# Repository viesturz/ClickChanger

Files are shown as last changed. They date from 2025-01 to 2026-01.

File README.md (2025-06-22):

# What is this?

A minimalistic 3d printer toolhead design, build from ground up for tool changing and primarily the Voron Family of printers.
Inspired by [Tapchanger](https://github.com/viesturz/tapchanger) and [Stealthchanger](https://github.com/DraftShift/StealthChanger). But not getting into  [PitStop](https://mihaidesigns.com/pitstop3/) territory yet.

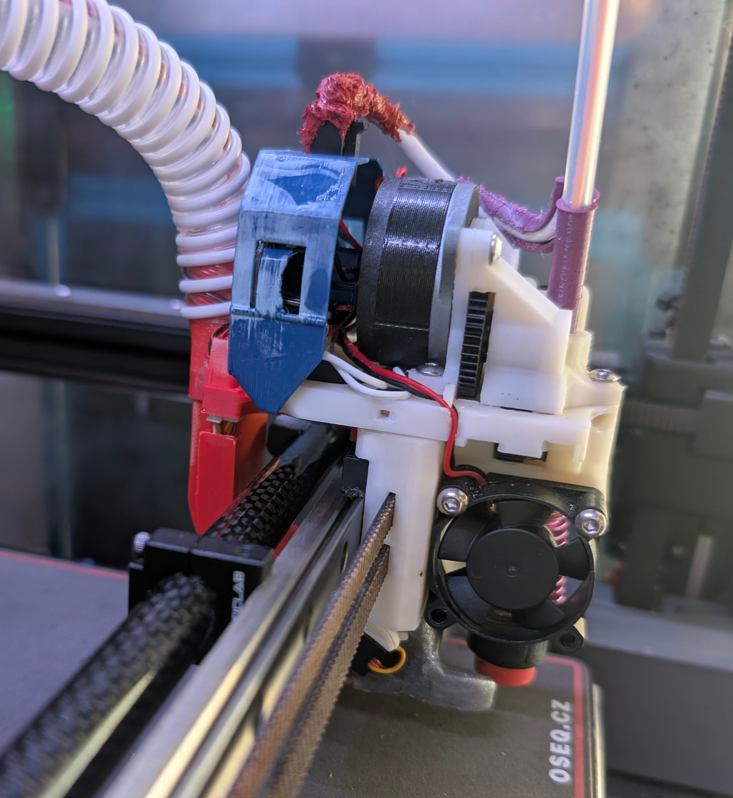
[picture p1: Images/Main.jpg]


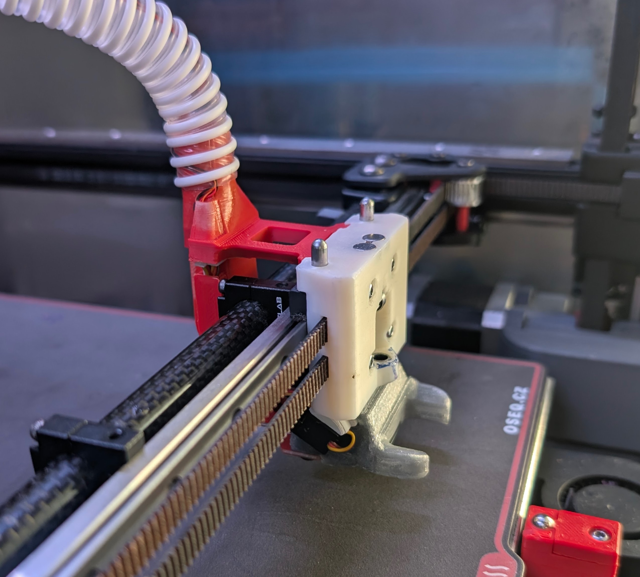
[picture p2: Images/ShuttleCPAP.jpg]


## How is this different?

ClickChanger is a yet another vertically attached design, but building on previous experiences, but here are some design directions it focuses on:
* A hotend based nozzle probe, like Revo PZ, not requiring the smooth vertical movement by the docking mechanism
* Rigid connection between the Y rail and hotend's heatsink, minimizing thermal expansion differences between toolheads
* A Shared part cooling fan integrated in the shuttle, connected via Pogo pins
* A "naked" toolhead, allowing for better cooling and overall less weight.

And keeping the features from other designs:

* Vertical motion to attach/detach the toolhead
* No wires to the shuttle, single cable to each toolhead

### Roadmap

Some of next directions this is going, in no particular order

* Documentation documentation documentation

### Contributing

Please file bugs and pull requests. My free time is quite limited, so will answer irregularly.
[Voron Toolchangers Discord](https://discord.com/invite/xmDWrYGwVJ) has lots of toolchanger users.
Also check out the [Youtube channel](https://www.youtube.com/playlist?list=PLqU7kX5nUJDT31KPcYAykZ2nuPKu_lhjn).

# Supported hotends

* Revo Voron
* Dragon or Dragon High flow
* Rapido HF (not the UHF)

# Supported bed probes
 * Revo PZ on T0
 * Beacon probe (low profile)
 * Cartographer probe (low profile)

# Supported extruders

* HGX Large Gears - personal favorite of mine, great for flexibles; lowest weight and integrated strain relief.
* HGX Large Gears V2
* Orbiter V2
* Sherpa mini and compatibles

# Supported toolboards
* Bitgtreetach EBB36 and compatibles
* Mellow Fly SHT36 V2 and Pro
* LDO Nitehawk (untested)

# BOM

**Common consumables**

* M3 screws, button head preferrably, 8mm and some other sizes
* M3x5x4 heatset inserts (voron spec)
* superglue, small tip tube, low viscosity

**Shuttle**

* a CPAP fan
* ~1m 15mm diameter tube
* a 3x6x2.5mm bearing (3x6x3 works too)
* a 2gram micro servo, DSPOWER has worked well for me
* 2 m2x4 screws
* some servo wire

**Toolhead**

* A supported extruder, toolhead, toolboard
* 1x 4mm x12mm round end steel pin
* 2x 4x6x6 mm bushing; preferrably the hybrid bushings for smoother slide
* a Kailh Micro switch or compatible 3mm tall momentary switch
* 30x30x10 or 30x30x7 axial fan for hotend cooling
* 1x m2x6 **socket head** screw
* 2x 6x3mm magnets

**Dock**

* 30 mm of 7x0.1mm springsteel, salvageable from 1m tape measure.
* High temp silicone for the nozzle pad

# Assembly instructions

* [CPAP valve](CPAP.md)
* See [TapChanger](https://github.com/viesturz/tapchanger) for my docking/wiring setup.
* See [Klipper-Toolchanger](https://github.com/viesturz/klipper-toolchanger/) for klipper firmware, [example config](https://github.com/viesturz/klipper-toolchanger/tree/main/examples/probe%20on%20T0).

More coming up

# Revision log

## 2.0 - CPAP is mandatory now.

Not compatible with previous versions, you will need to reprint everything, except docks and need a new microswitch.

* Only CPAP supported, the airflow is just so much better.
* More rigid shuttle, going from 6 to 8 mm width, extra side walls.
* Using a slimmer 3mm tall microswitches for tool detection
* Some supports modelled
* Remodelled PTFE tube connector
* Better toolboard cages
* Best part is no part - no more retaining clips
* Tensioning screw position adjusted for slightly less click and more tension

## 1.1.1 - Small tweaks and cleanups.

## 1.1 - CPAP edition

* CPAP and eddy current probe support.
* Docks slightly redesigned, added magnets in docks.

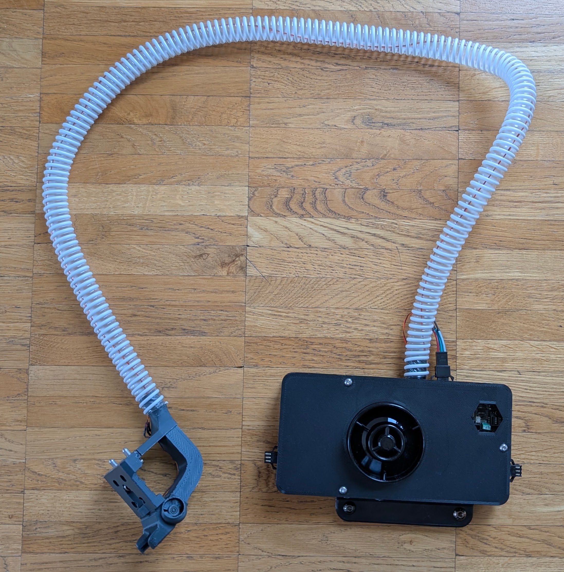
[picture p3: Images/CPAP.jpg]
CPAP
}

## 1.0 - Fingers crossed

The first one that is ready to be beta tested. **Not compatible with previous ones** the shuttle interface has changed.

Added: 
* Rigid mount dock initial version
* CPAP initial version

Small refinements across the board

## 0.9 - Small improvements

Added:

* Rapido extruder base
* Nitehawk toolbard cage

Small refinements across the board:

* HGX Lite gears 2 refinements
* Fan shroud refinements
* Better fit for some holes

## 0.8 - It prints!

Introduced pogo pins for the fan connection and a new wiring holder.

Full PTFE tube channel for HGX - better for flexibles.

Assembly is quite repeatable now.

Printing reasonably stable now, hundreads of toolchanges but still expect some warts.

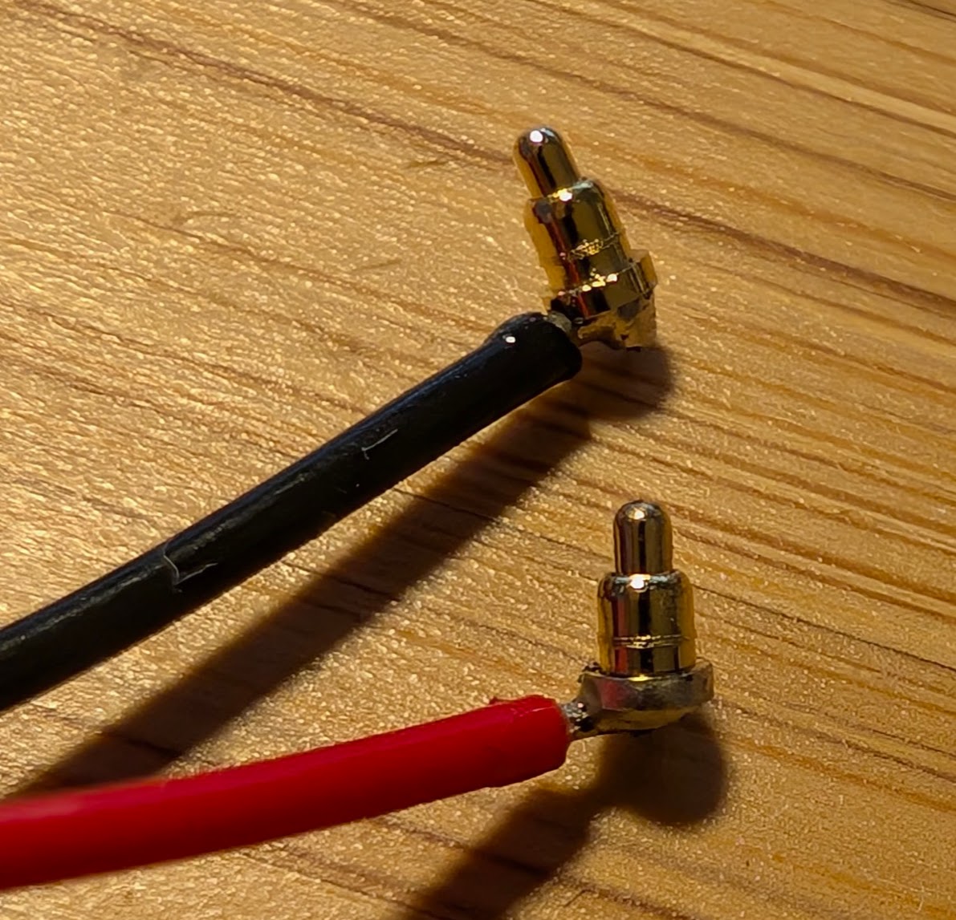
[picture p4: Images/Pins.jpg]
Pogo pins


## 0.1 - It clicks!

There is an initial BOM, the click force is good, assembly is repeatable, building two and putting to the test.

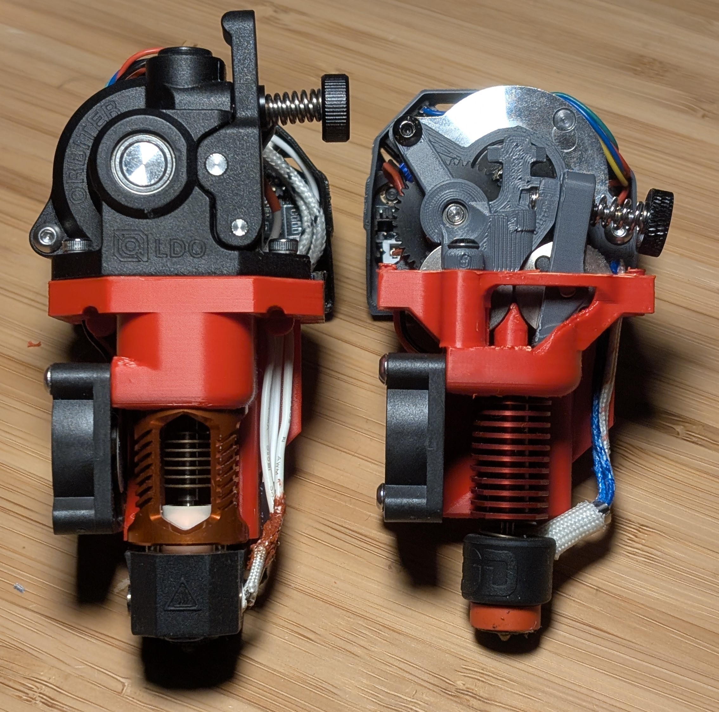
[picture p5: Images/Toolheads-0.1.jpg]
Toolheads

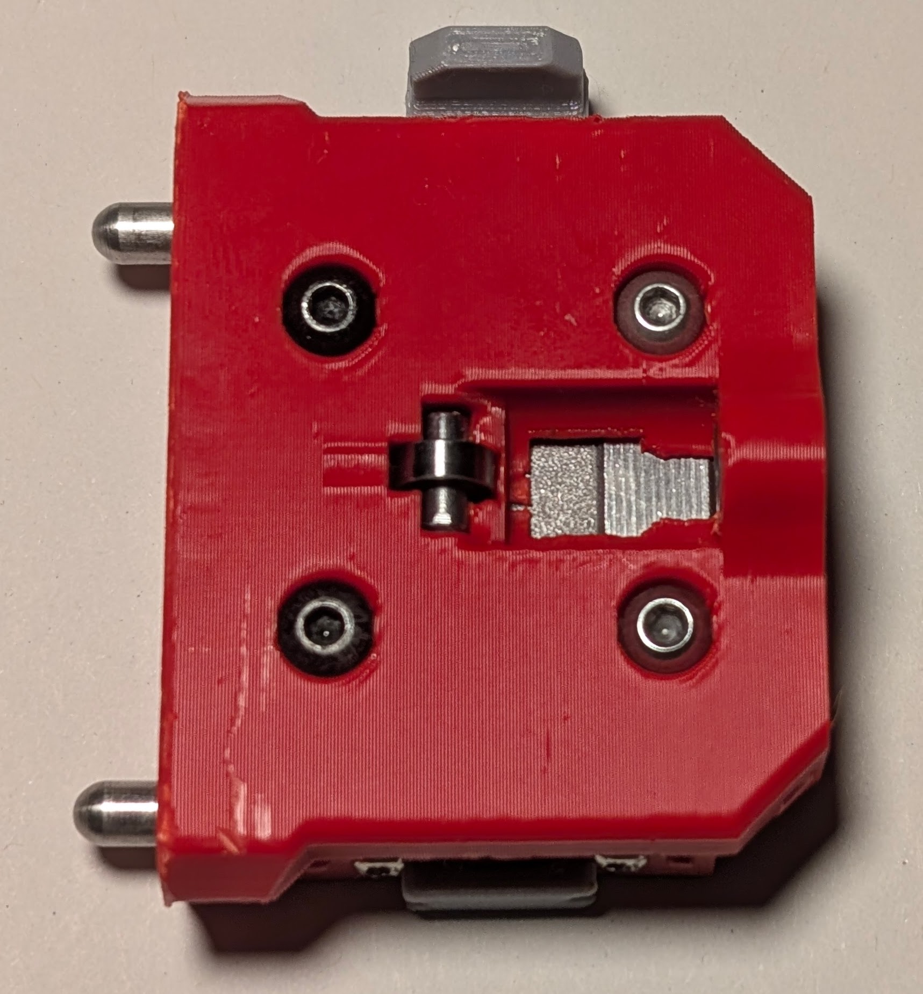
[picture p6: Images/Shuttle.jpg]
Shuttle


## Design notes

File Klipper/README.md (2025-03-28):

# Klipper integration

Please see [Klipper-Toolchanger](https://github.com/viesturz/klipper-toolchanger/)

## CPAP

Feel free to adapt my [CPAP config](./CPAP_mcu.cfg). That is based on a dedicated toolbard.
You will need to change the pin assignment if you are using something else..

Please file a bug if you are interested in detailed build instructions for the CPAP box.

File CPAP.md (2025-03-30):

# Valve installation

The valve installation is tricky by the fact that the servos have no stop point so getting the valve angle right is difficult. 

Start by powering on the servo and set the angle to 90 degrees so that it's at known angle.

Then attach the shim and press on the valve so that it aligns with the shim.
Once pressed on, secure the valve with a screw or a bit of superglue. It will rattle loose otherwise.

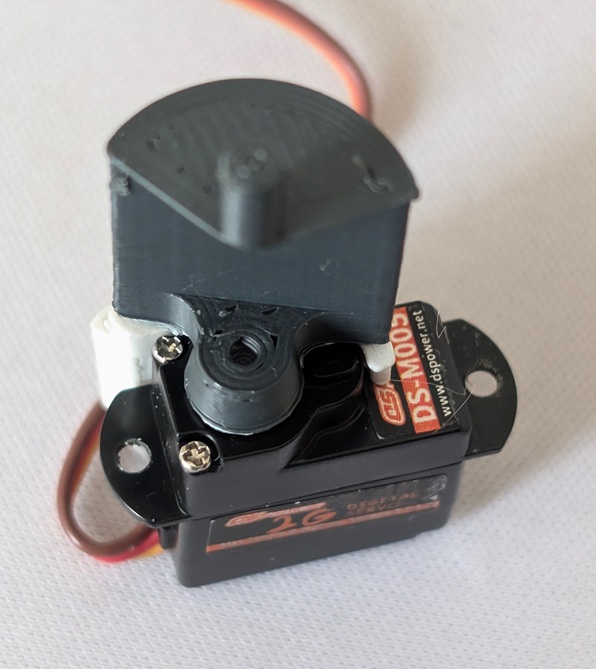
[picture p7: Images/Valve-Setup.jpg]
Valve setup


Then install the bearing on the opposite side.

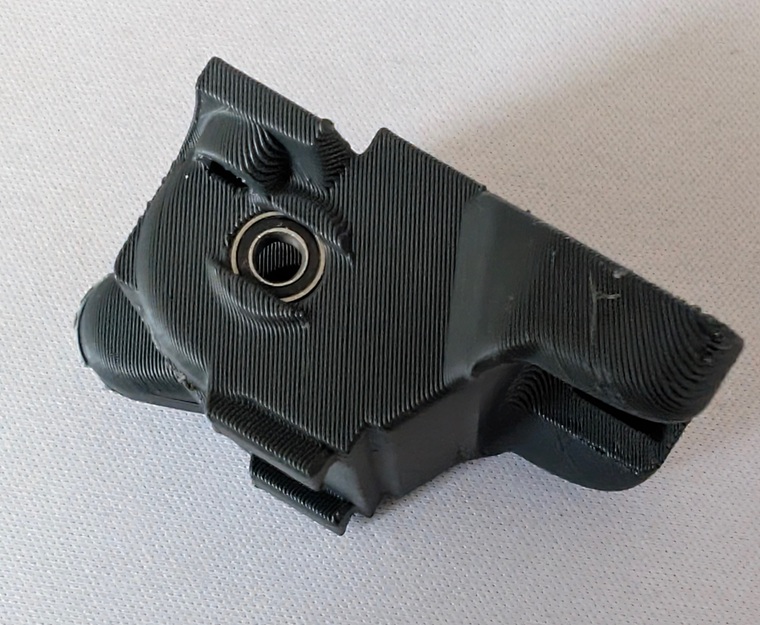
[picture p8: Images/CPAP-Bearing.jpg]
Bearing


Then carefullly push the valve assembly into the shroud. Note the servo wire routing.

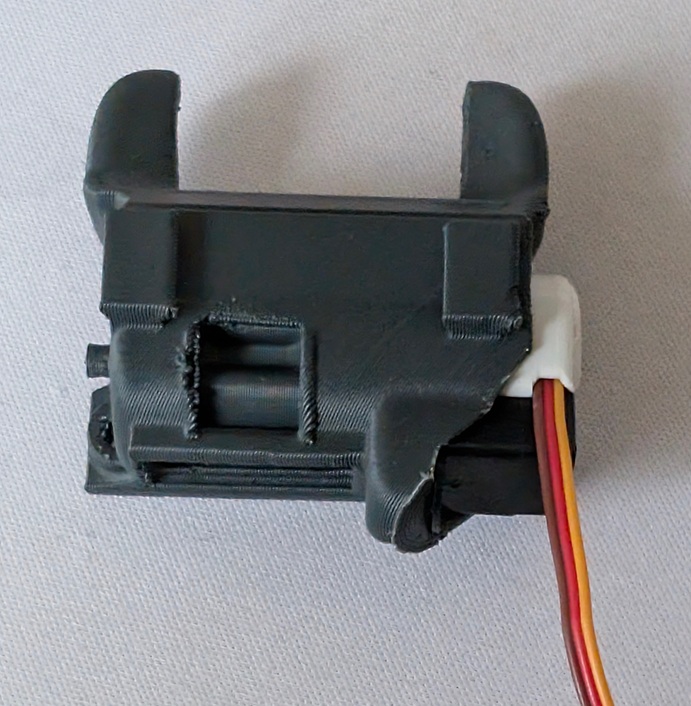
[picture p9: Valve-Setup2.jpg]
Valve assembed


And secure with 2 M2 x4 screws.

## Fine tuning the servo angle.

90 degrees is your fully open angle. And fully closed should be about 165 degrees, but will depend on your servo, so test and adjust as necessary.

See [Example klipper config](Klipper/CPAP_mcu.cfg)  for valve and CPAP control

| Valve open  | Valve closed |
| --- | --- |
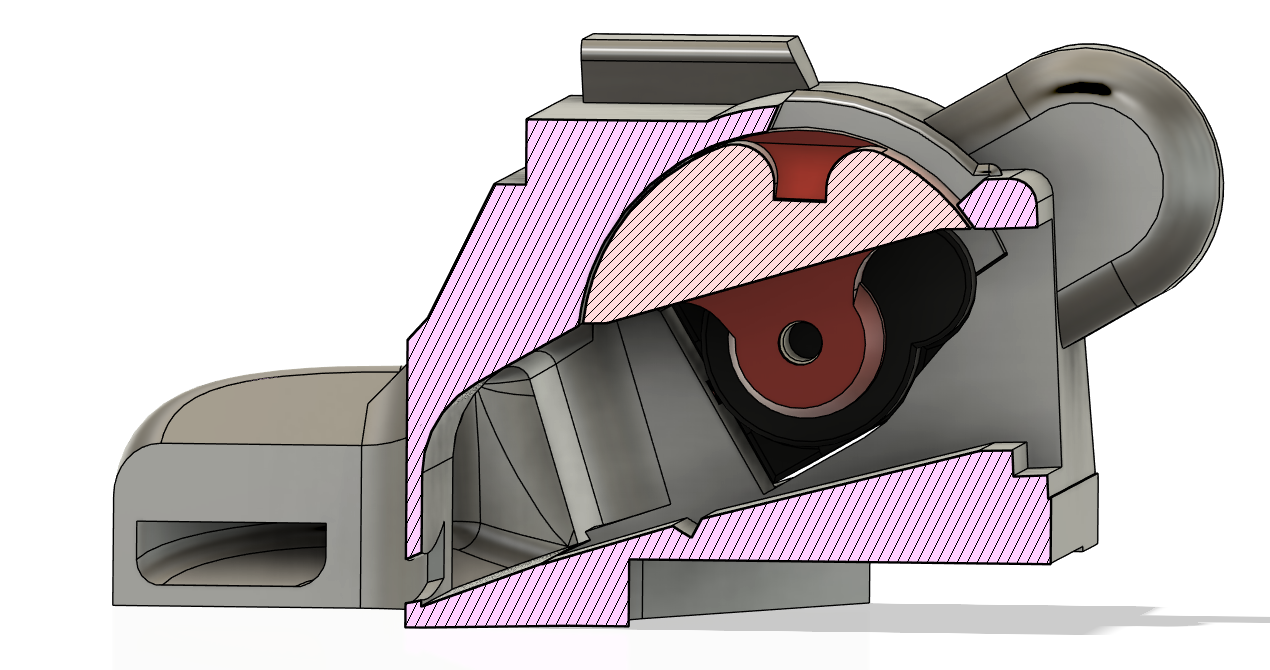
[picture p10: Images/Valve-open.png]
Open
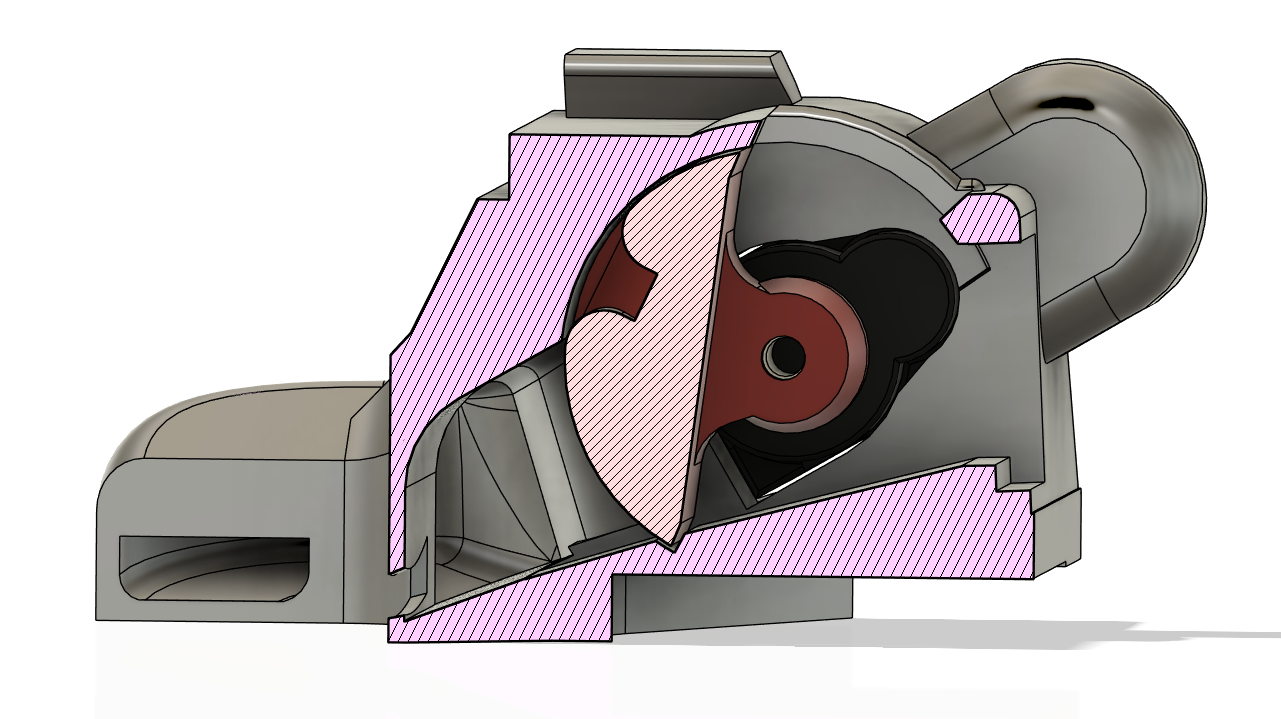
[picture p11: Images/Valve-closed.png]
Closed
|   |  |

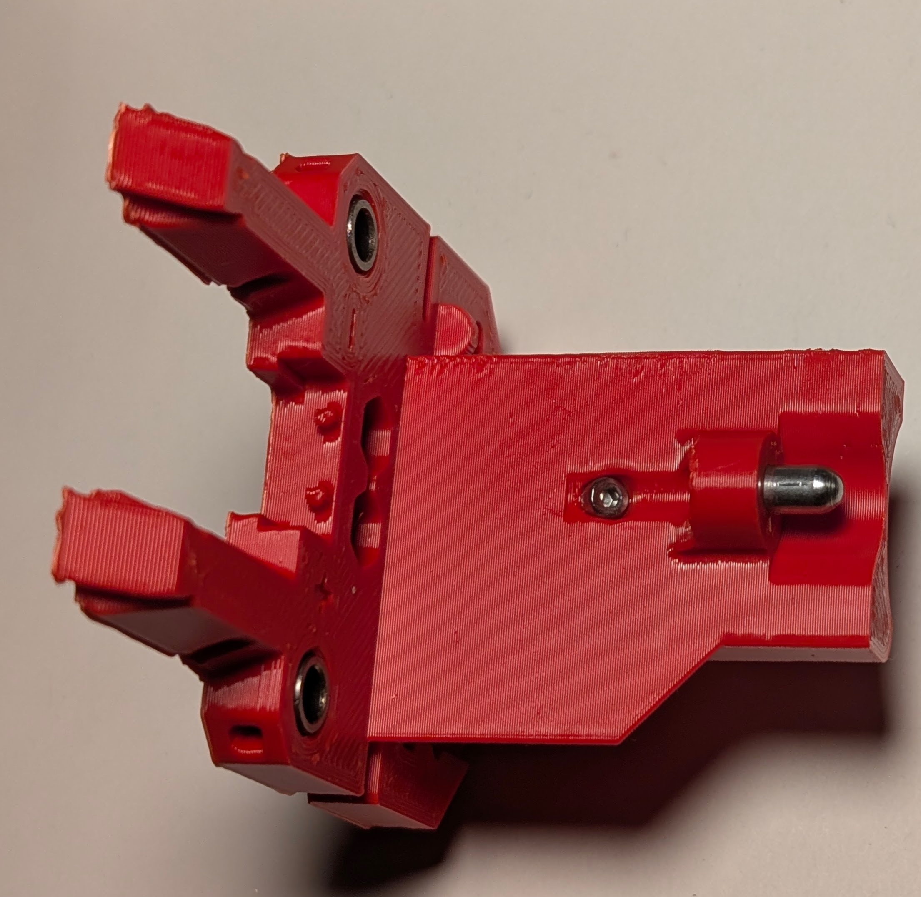
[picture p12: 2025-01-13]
Images/ToolheadPart.jpg

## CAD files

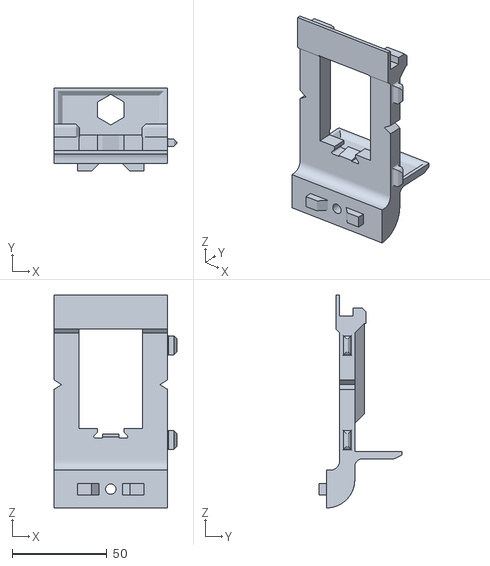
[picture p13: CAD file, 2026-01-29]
BearingsVariant/Dock/Dock Liftbar.obj
65.0 x 44.0 x 112.6

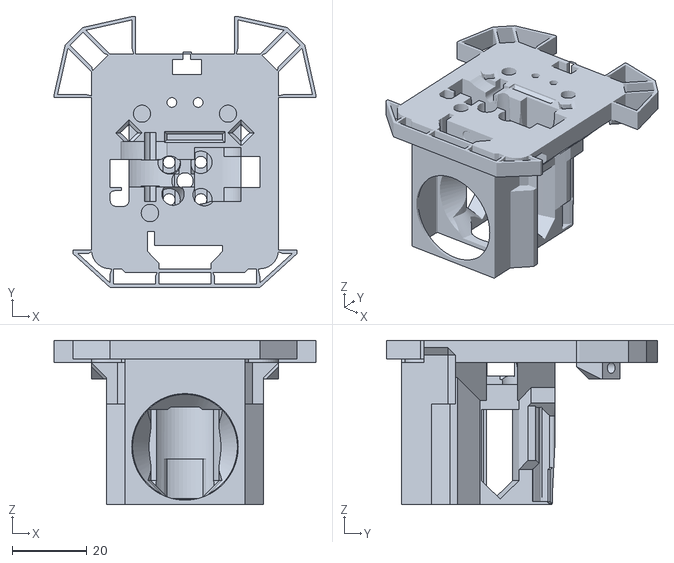
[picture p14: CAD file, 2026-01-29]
BearingsVariant/Hotends/Base Revo.obj
70.0 x 72.5 x 44.0

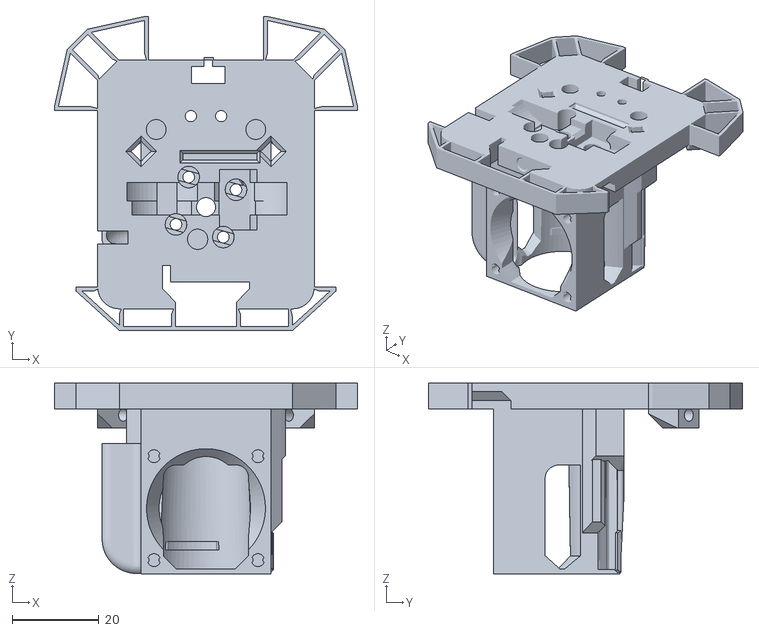
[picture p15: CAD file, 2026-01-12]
BearingsVariant/Hotends/Rapido/Base Rapido.obj
70.0 x 72.5 x 44.1

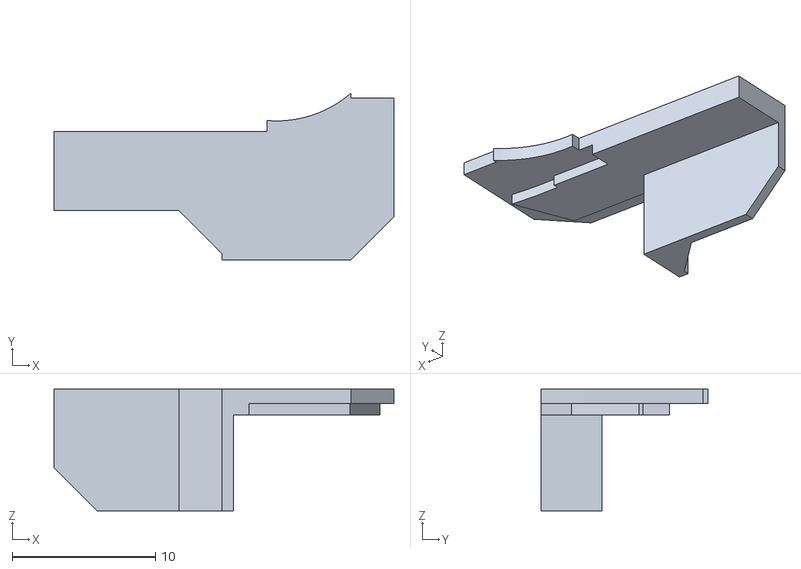
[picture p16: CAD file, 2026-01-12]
BearingsVariant/Shuttle/Wire Shield.obj
23.7 x 11.6 x 8.50

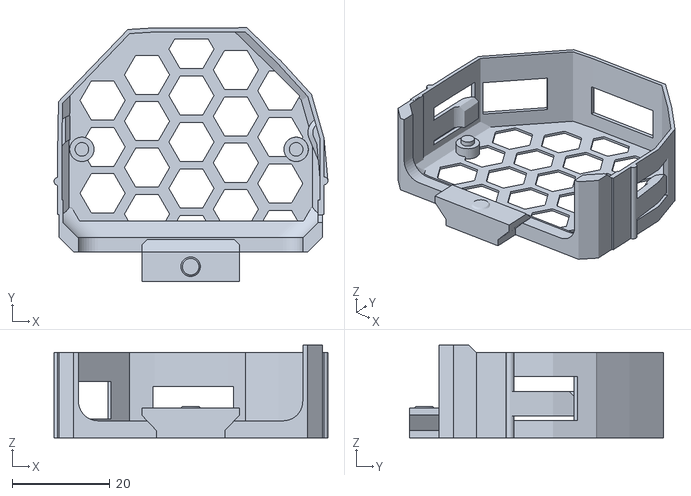
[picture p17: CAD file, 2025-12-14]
BearingsVariant/Toolbards/LDO nitehawk cage.obj
56.1 x 51.9 x 19.0

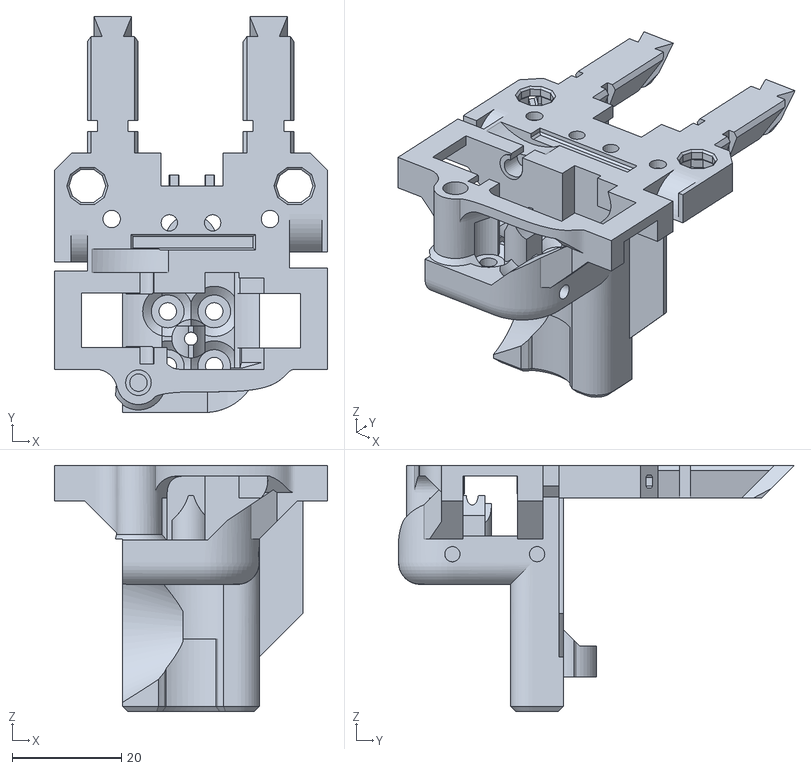
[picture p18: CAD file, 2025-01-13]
Cores/HGX Gears + Revo/Core Revo.obj
50.0 x 72.5 x 45.1

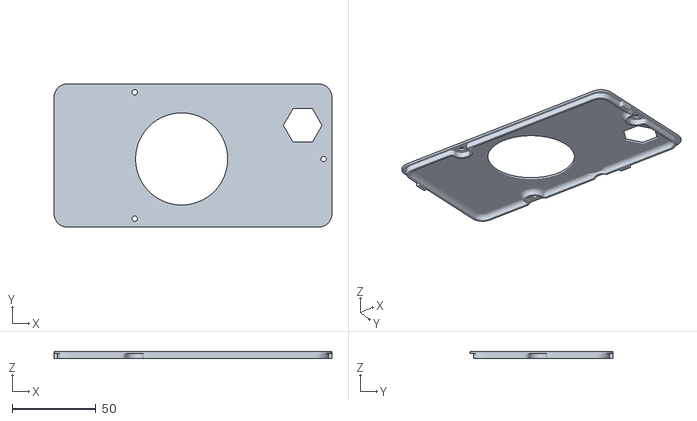
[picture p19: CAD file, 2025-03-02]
CPAP/WS7040 mount/Lid.obj
166.0 x 85.5 x 4.00

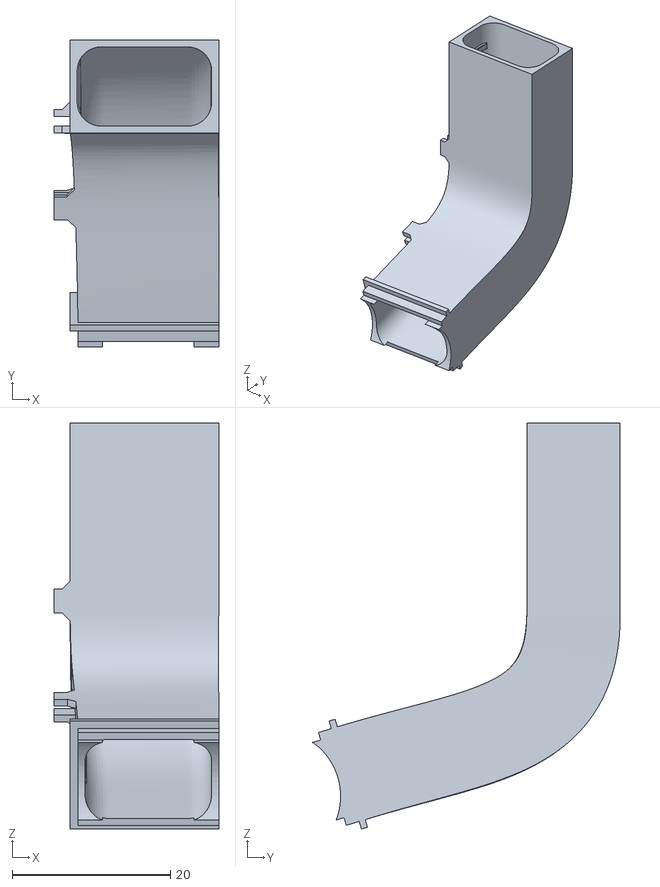
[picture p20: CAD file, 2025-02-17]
Extras/CPAP/Tube.obj
20.8 x 38.8 x 51.3

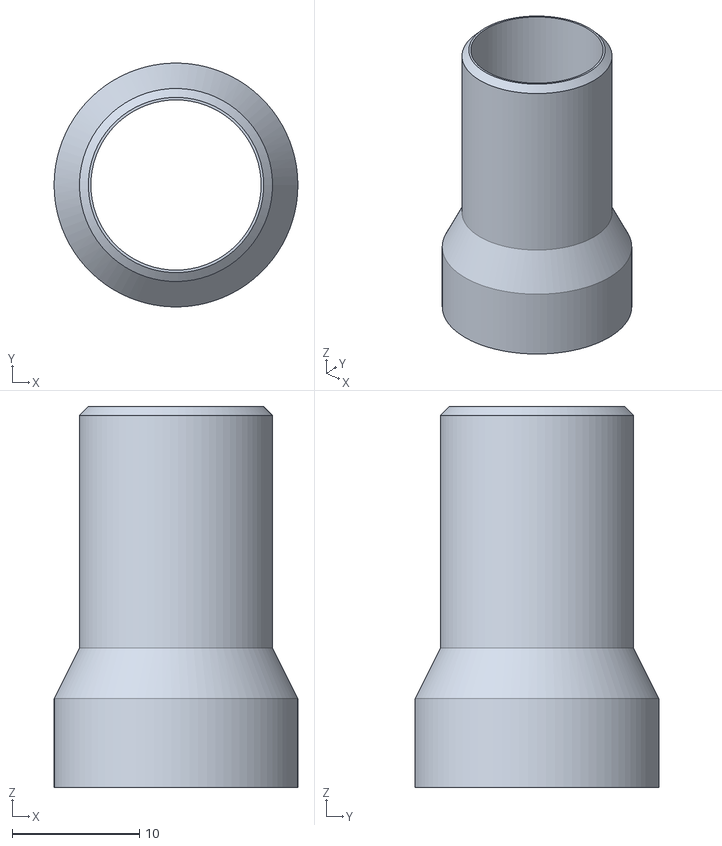
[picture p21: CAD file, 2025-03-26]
Extras/WS7040 mount/Tube Adapter.obj
19.2 x 19.2 x 30.0

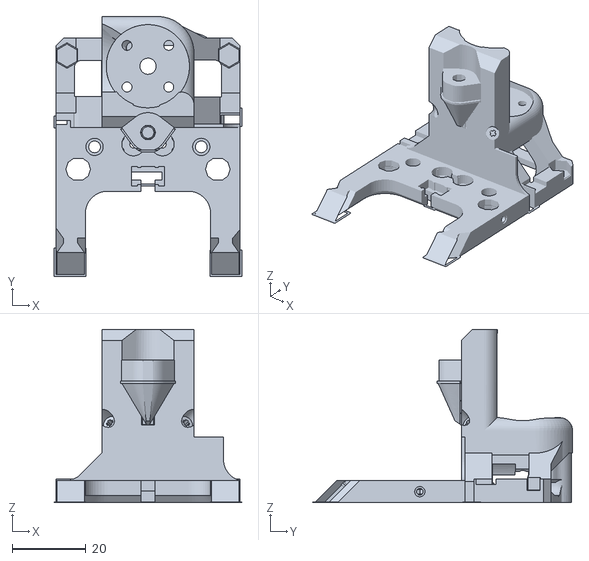
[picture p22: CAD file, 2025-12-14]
PinsVariant/Cores/Dragon + HGX Gears.obj
51.0 x 70.6 x 47.1

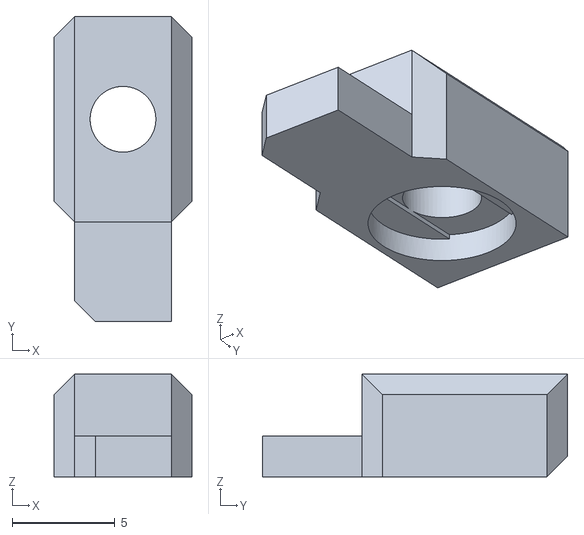
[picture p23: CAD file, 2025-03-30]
PinsVariant/Dock/HGX Dock Pin.obj
6.70 x 14.8 x 5.00

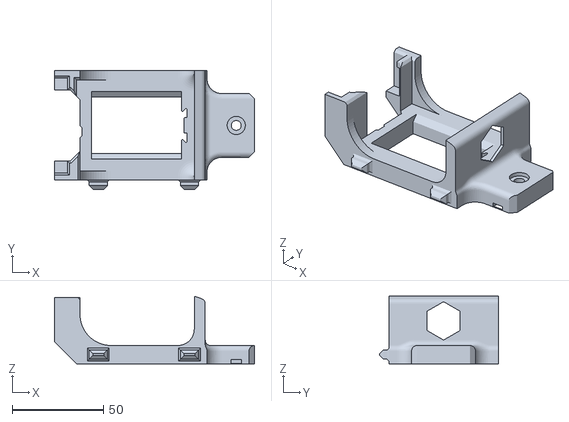
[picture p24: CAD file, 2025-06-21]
PinsVariant/Dock/Liftbar/Dock HGX.obj
109.6 x 65.0 x 37.0

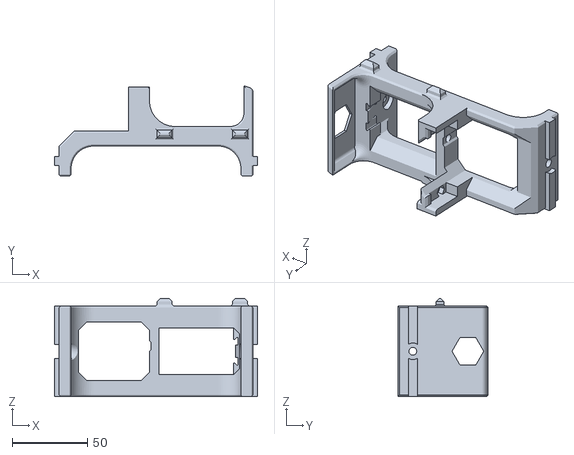
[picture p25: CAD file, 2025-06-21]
PinsVariant/Dock/Rigid/Dock HGX.obj
134.6 x 60.0 x 65.0

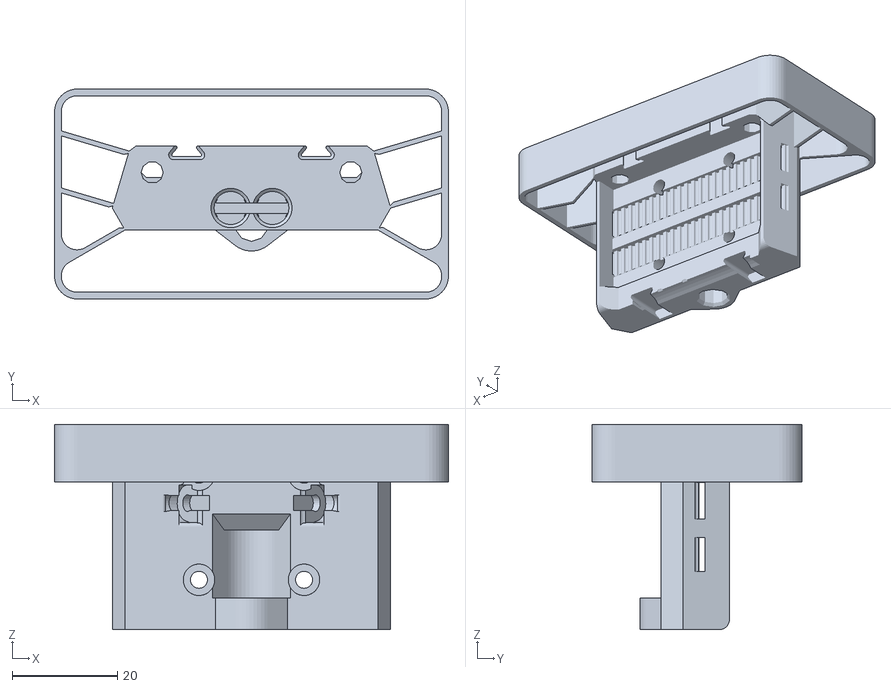
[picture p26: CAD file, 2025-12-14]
PinsVariant/Shuttle/Shuttle.obj
75.0 x 40.0 x 39.1

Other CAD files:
Shuttle + CPAP + Eddy current probe/Connector.obj
Tools/Shuttle pin helper.obj
Tools/Test fixture/MGN12H fixture.obj
BearingsVariant/Dock/Wipe Clip.obj
Archive/Shuttle + 4010/4010 Fan Shroud.obj
Archive/Shuttle + 4010/Shuttle.obj
BearingsVariant/Dock/Dock Rigid.obj
BearingsVariant/Hotends/Base Dragon.obj
BearingsVariant/Hotends/Gear housing.obj
BearingsVariant/Hotends/Lever.obj
BearingsVariant/Hotends/Motor Mount.obj
BearingsVariant/Hotends/Rapido/Gearbox Rapoido.obj
BearingsVariant/Hotends/Rapido/Lever Rapido.obj
BearingsVariant/Hotends/Rapido/Motor Mount Rapido.obj
BearingsVariant/Hotends/Tube holder 5mm.obj
BearingsVariant/Shuttle/Cooling Duct.obj
BearingsVariant/Shuttle/Plug.obj
BearingsVariant/Shuttle/Shuttle Heatset stand.obj
BearingsVariant/Shuttle/Shuttle.obj
BearingsVariant/Shuttle/Valve Body.obj
BearingsVariant/Shuttle/Valve.obj
BearingsVariant/Shuttle/ValveBody.obj
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

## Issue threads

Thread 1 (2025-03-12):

ebb36 cage, doesn't fit

sn3akyly, 2025-03-12:
the ferrule connectors for hotend power are blocking the ebb36-cage from fitting into the main part

viesturz, 2025-03-28:
Yeah, I ran into the same issue at one point.
The simplest solution is to not use ferrules 🙃
I will keep this in mind next time there is a significant design change. The location of the two fingers is quite central of the entire design and not that easy to move around.

sn3akyly, 2025-03-29:
yes I noticed ^^
Decided to just give the cage 5mm more in the Z, works with the ferrules like a charm and doesn't interfere with anything on my setup this far

viesturz, 2025-06-18:
A new version is coming soon (a few days).

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

dlhenke, 2025-06-22:
> A new version is coming soon (a few days).
> […](#)

Put also the Revo + sherpa mini.
Also if possible the step files with no compound ..
Just downloaded the files today .. started to print right now .

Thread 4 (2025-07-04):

CAD missing parts

leezus-nz, 2025-07-04:
Hi, Unfortunately the .step file seems to have exported poorly.

It's also missing the extruder for the 9mm gears.

Is it possible to re-export the file please.

Thanks

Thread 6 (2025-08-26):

List of components for the assembly ClickChanger

demonically, 2025-08-26:
I studied your files in the repository and noticed that in BOM several components, such as the pin of the bearing in the shuttle. This is what a list of materials I have compiled

**Common consumables**

- M3 screws, button head preferrably, 8mm and some other sizes
- M3x5x4 heatset inserts (voron spec)
- superglue, small tip tube, low viscosity

**Shuttle**

- CPAP fan (WS7040, BTT Turbo...)
- ~ 1m CPAP Tube with diameter 5mm
- 3x6x2.5 bearing (ex. MR83ZZ )
- m3x8 pile for attaching the bearing
- 2g microservo (ex. DSPOWER)
- 2x m2x4 screws
- 2x steel pin 4x12 with round end
- 4x6x6 bushing (pref. hybrid for smoother slide)
- 2x 6x3mm magnets
- some servo wire

**Toolhead**

- supported extruder (ex. Sherpa...)
- supported toolhead (ex. Dragon HF...)
- supported toolboard (ex. EBB36...)
- 1x 4x12 mm's steel pin with round end
- 2x 4x6x6 mm's bushing (pref. hybrid for smoother slide)
- a Kailh Micro switch / compatible 3mm tall momentary switch with sizes like 3 mm x 8.6 mm x 4.8 mm
- 3010 or 3007 axial fan for hotend cooling
- 1x m2x6 socket head screw
- 2x 6x3mm magnets

**Dock**

- 30 mm of 7x0.1mm springsteel (salvageable from 1m tape measure
- High temp silicone for the nozzle pad

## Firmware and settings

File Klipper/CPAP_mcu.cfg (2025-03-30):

# This file contains common pin mappings for the BIGTREETECH EBBCan
# Canbus board. To use this config, the firmware should be compiled for the
# STM32G0B1 with "8 MHz crystal" and "USB (on PA11/PA12)" or "CAN bus (on PB0/PB1)".
# The "EBB Can" micro-controller will be used to control the components on the nozzle.

# See docs/Config_Reference.md for a description of parameters.

[mcu mtop]
canbus_uuid: 1a3c230191ed

[neopixel led]
pin: mtop:PD3
chain_count: 21
color_order: GRB
initial_RED: 0.0
initial_GREEN: 0.0
initial_BLUE: 0.0

[fan_generic cpap]
pin: mtop:PB9
shutdown_speed:0
cycle_time:0.01

[servo fan]
pin: mtop:PB8
maximum_servo_angle: 180
minimum_pulse_width: 0.0005
maximum_pulse_width: 0.0025

[gcode_macro CPAP_STOP]
gcode:
  SET_FAN_SPEED FAN=cpap SPEED=0.0
  SET_GCODE_VARIABLE MACRO=M106 VARIABLE=cpap_power VALUE=0.0

[gcode_macro M106]
variable_cpap_power: 0.0
gcode:
  {% set min_cpap = 0.2 %}
  {% set max_cpap = 0.7 %}
  {% set current_cpap = printer['gcode_macro M106'].cpap_power|float %}
  {% set speed = params.S|float / 255.0 %}
  {% set zero_angle = 165 %}
  {% set min_angle = 165 %}
  {% set max_angle = 90 %}
  {% if speed < 0.01 %}
    # Almost zero - close the valve fully
    SET_SERVO SERVO=fan ANGLE={ zero_angle }
  {% elif speed <= current_cpap %} 
    # CPAP fan is already at sufficient power - modulate the valve
    {% set valve_position = speed / current_cpap %}
    SET_SERVO SERVO=fan ANGLE={ min_angle + (max_angle-min_angle) * valve_position }    
  {% else %}
    # Need more power - ramp up the CPAP
    {% set valve_position = 1.0 %}
    SET_GCODE_VARIABLE MACRO=M106 VARIABLE=cpap_power VALUE={ speed }    
    SET_FAN_SPEED FAN=cpap SPEED={ min_cpap + speed * (max_cpap - min_cpap) }
    SET_SERVO SERVO=fan ANGLE={ min_angle + (max_angle-min_angle) * valve_position } 
  {% endif %}

[gcode_macro M107]
gcode:
  M106 S0

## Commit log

2025-01-13 Initial version 0.1
    [4010 Fan Shroud.obj, Core Revo.obj, Dock Liftbar spacer.obj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]
2025-01-14 Dock tweaks
    [Dock HGX.obj, Dock Regular.obj, Dock-HGX.obj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]
2025-01-14 More room for switch wiring
    [4010 Fan Shroud.obj, Gear housing.obj, Lever.obj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]
2025-01-27 Next iteration, lots of minor changes.
    [4010 Fan Shroud.obj, 6mm belt clip x2.stl, 9mm belt clip x2.stl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]
2025-02-02 Updated HFX extruder with full length PTFE tube and strain relief.
    [Dock HGX.obj, EBB36 cage.obj, Fly SHT36 V2 cage.obj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]
2025-02-03 More robust wire clip; adding Dragon version for all.
    [Dragon + HGX Gears.obj, Dragon + Sherpa.obj, Dragon PTFE tube jig left.obj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]
2025-02-09 V 0.8 is a wrap.
    [Dock HGX.obj, Dock Regular.obj, Dragon + HGX Gears 2.obj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]
2025-02-11 HGX Gears 2 tweaks
    [Dragon + HGX Gears 2.obj, Gear housing.obj, Lever.obj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]
2025-02-13 CAD updates
    [Dock Regular.obj, Rapido + Orbiter2.obj, Revo + HGX Gears 2.step]
2025-02-14 Add Nitehwak cage
    [Fly SHT36 pro cage.obj, LDO nitehawk cage.obj, Wire clip.obj]
2025-02-17 Add CPAP option
    [Connector.obj, Exhaust.obj, Shroud.obj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]
2025-02-19 Update cable holder; swap heatset insert side for HGX gears2
    [Dragon + HGX Gears 2.obj, Revo + HGX Gears 2.obj, [TPU] Cable flex Extruder.obj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]
2025-02-21 Add 5mm tube option
    [Gear housing.obj, [TPU] Wire flex 4mm tube.obj, [TPU] Wire flex 5mm tube.obj]
2025-02-21 Update CAD
    [Gear housing.obj, Revo + HGX Gears 2.step]
2025-02-23 Rigid dock
    [Dock HGX.obj, Dock Regular.obj, Dock.obj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]
2025-02-24 Recess the nicroswitch 2mm to reduce crash damage
    The microswitch got repeatedely destroyed when the docking sequence goes wrong.
    So recessing it as much as possible into the toolhead to minimize the chance of hitting it.
    This is an INCOMPATIBLE change, need a new shuttle and all the toolheads.
    [Connector.obj, Dragon + HGX Gears 2.obj, Dragon + HGX Gears.obj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]
2025-02-24 Close up a unneeded gap in HGX 2
    [Dragon + HGX Gears 2.obj, Revo + HGX Gears 2.obj]
2025-02-24 Move files around
    [Connector.obj, Dragon PTFE tube jig left.obj, Dragon PTFE tube jig right.obj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]
2025-03-02 Add belt helper
    [6mm belt clip x2.stl, 9mm belt clip x2.stl, Left Side.stl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]
2025-03-02 Add CPAP fan mount
    [Base.obj, Lid.obj, Tube clip.obj]
2025-03-02 Slimmer wire clip
    [Wire clip.obj]
2025-03-02 Wider filament intake guide
    [Gear housing.obj]
2025-03-02 CPAP tweaks
    [Exhaust.obj, Shroud.obj, Valve.obj]
2025-03-02 Shuttle: Tune the tool switch groove
    [Shuttle.obj]
2025-03-02 Fix connector to have room for the X gantry corner pieces.
    [Connector.obj]
2025-03-02 Beef up the lever
    [Lever.obj]
2025-03-04 Move folders around & some tweaks
    [Base.obj, Connector.obj, Dock HGX.obj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]
2025-03-07 Move files around again. Add angled bracket for rigid dock
    [Base.obj, Connector.obj, Dock Angled bracet.obj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]
2025-03-16 HGX2 fix
    [Gear housing.obj]
2025-03-16 CPAP WIP
    [4010 Fan Shroud.obj, Base.obj, Connector.obj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]
2025-03-16 Update CPAP cooler based on Eddy probe design.
    [4010 Fan Shroud.obj, Connector.obj, Exhaust.obj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]
2025-03-16 Tube tweaks
    [Tube.obj]
2025-03-16 Add basic CPAP, no servo
    [Connector.obj, Servo Insert.obj, Shroud.obj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]
2025-03-18 Update servo insert.
    [Servo Insert.obj, Shroud.obj, Shuttle.obj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]
2025-03-22 CPAP valve rework
    - Exhaust moved from side to top, making the valve smaller and simpler. And allowing more plastic between the valve and probe PCB.
    - connectors changed to JST 1.25 - the 1.0 are really fiddly to work with.
    - integrated supports for the tube.
    - overall polish.
    [Connector.obj, Servo Insert.obj, Servo shim.obj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]
2025-03-23 Add tube adapter
    [Tube Adapter.obj]
2025-03-23 Add a wire cover
    [Tube Wire cover.obj, Tube.obj]
2025-03-24 Update the dock design for HGX
    [Dock HGX.obj, Dragon + HGX Gears 2.obj, Dragon + HGX Gears.obj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]
2025-03-26 Tweaks to the fan mount
    [Dock HGX.obj, Lid.obj, Tube Adapter.obj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]
2025-03-27 HGX gears 2 - update to match the dock design
    [Dragon + HGX Gears 2.obj, Revo + HGX Gears 2.obj]
2025-03-28 CPAP tweaks, CAD update.
    [Dock HGX.obj, Dragon + HGX Gears.obj, Revo + HGX Gears 2.step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]
2025-03-28 1.1 it is.
    [CPAP_mcu.cfg]
2025-03-29 Add optional dock pin
    [Dock HGX.obj, HGX Dock Pin.obj]
2025-03-30 CPAP instructions, tweaks to the CPAP connector.
    [CPAP_mcu.cfg, Connector.obj, HGX Dock Pin.obj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]
2025-03-30 Servo CPAP - Narrowed vent hole to have roughly the same pressure as the shroud.
    [Shroud + Servo + Cartographer probe.obj, Shroud + Servo + Cartographer.obj, Shroud + Servo.obj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]
2025-03-31 Small tweaks.
    [4010 Fan Shroud.obj, Connector.obj, Dock HGX.obj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]
2025-04-02 Printablility tweaks
    [Dragon + HGX Gears 2.obj, Revo + HGX Gears 2.obj]
2025-04-12 Add a bit more space for stepper motor, it's a bit tight.
    [Gear housing.obj, Motor mount.obj]
2025-04-12 Experimental Bambu hotend
    [Bambu + HGX Gears 2.obj]
2025-06-21 Fix GHX2 tube holder
    [Gear housing.obj]
2025-06-22 Update images and tube support back.
    [Tube.obj]
2025-07-05 HGX gears: Move dock magnets a bit to have more clearance.
    [Dragon + HGX Gears.obj, Revo + HGX Gears.obj]
2025-08-02 Toolboard cages - extend the lip to fill in the gap fully and reinforce a bit.
    [EBB36 cage.obj, Fly SHT36 V2 cage.obj, Fly SHT36 pro cage.obj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]
2025-08-03 Update shuttle pin helper to work better with new shuttle.
    [Shuttle pin helper.obj]
2025-12-14 Prepare space for bearings variant
    [Dock Angled bracet.obj, Dock HGX.obj, Dock Regular.obj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]
2025-12-14 Add Bearings files
    [Base Dragon.obj, Base Rapido.obj, Base Revo.obj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]
2025-12-20 Tweak the motor wire clip
    [Motor Mount.obj]
2026-01-12 Bearings variant updates.
    New CPAP valve and duct, rigid dock, better hotend wire routing.
    [Base Dragon.obj, Base Rapido.obj, Base Revo.obj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]
2026-01-29 Barings variant: * Fan housing added * Redone dock to fit the new fan housing * Gear housing has a wall to keep wiring in the cage.
    Shuttle unchanged, toolheads need full reprint.
    [Base Dragon.obj, Base Revo.obj, Dock Liftbar.obj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]
